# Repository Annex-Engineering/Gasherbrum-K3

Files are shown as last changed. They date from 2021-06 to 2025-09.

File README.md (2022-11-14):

# Gasherbrum (K3) Printer - Release 1.1

Project Gasherbrum (K3 for short) is a Small Format, Direct Drive, Fully Enclosed or Open Air FDM Printer.

This is an entirely scratch design, based on the efforts of the "Hypercube Overkill Project" for the XY Motion System, and inspired by all other prior repraps.

Our discord server can be found here: 

Join me on Discord (https://discord.gg/MzTR3zE)

BOM/Sourcing Guide can be found here: https://docs.google.com/spreadsheets/d/1O3eyVuQ6M4F03MJSDs4Z71_XyNjXL5HFTZr1jsaAtRc/edit?usp=sharing

# Project Goals:
- Fully Enclosed Design or Open Air
- 2020 Frame Members
- Build Volume of ~180^3 mm
- Direct Drive Extruder (Sherpa Mini, Sherpa Micro, and Folded Ascender supported)
- Shortest Belt Paths Possible, 4 Motors, 2 Per X, 2 Per Y Axis
- Moving Bed
- MGN9C Rails (XYZ and Cross)
- 9mm Belts on XYZ
- Maxwell Coupling on Bed Frame
- NEMA17 Motors XYZ
- LDO Stepper Motors (Optional but Recommended)
- Minimal Printed Parts (ABS/ASA Required)
- 32 bit controller standard (Single Fysetc Spider, or Fysetc S6 with expander configurations provided, others at your own leasure) - Klipper Highly Recommended
- 24V Power Standard, 48V Power Optional via the ANNEX Constellation Series of Boards
- AC Heated Bed, MIC6 Plate with Magnetic Build Surface or Glass on Thermal Pads
- Supports many hotends

* Enclosed Printers are passively heated and only designed around an average 65C chamber temperature, K3 is not intended to be a High Temperature printer. It was designed to excell at common engineering materials such as PLA, PETG, ABS and some PC/Nylon Blends

# Images
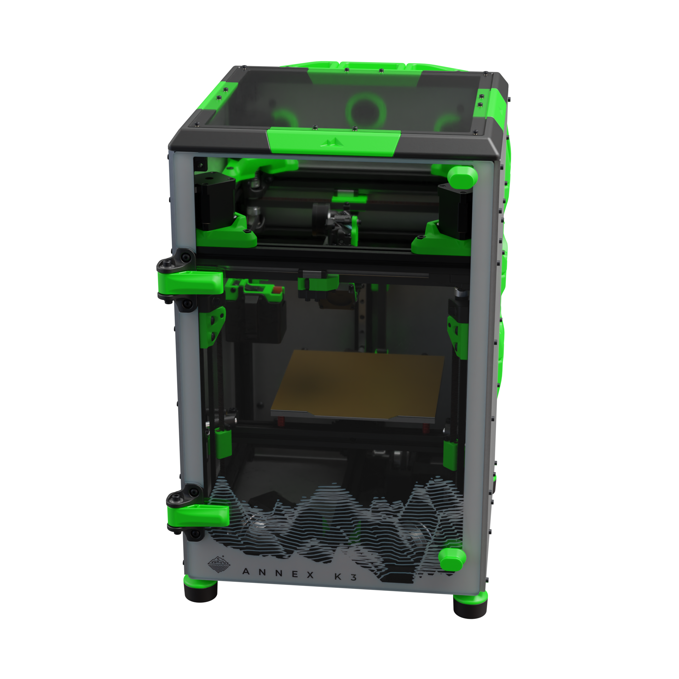
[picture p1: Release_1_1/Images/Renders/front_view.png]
Image of K3
 
  
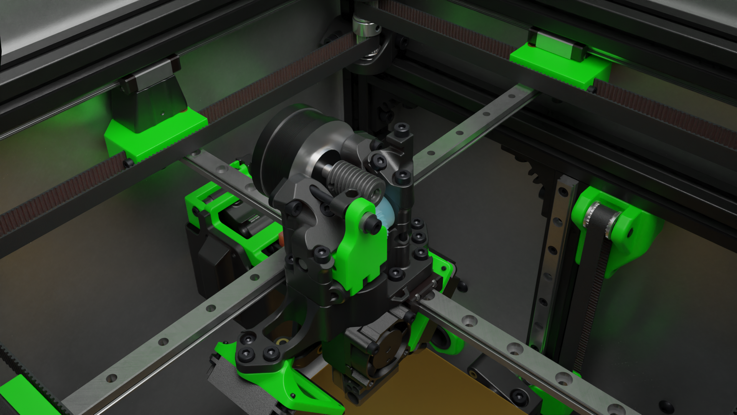
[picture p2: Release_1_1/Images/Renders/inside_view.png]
Image of K3
 

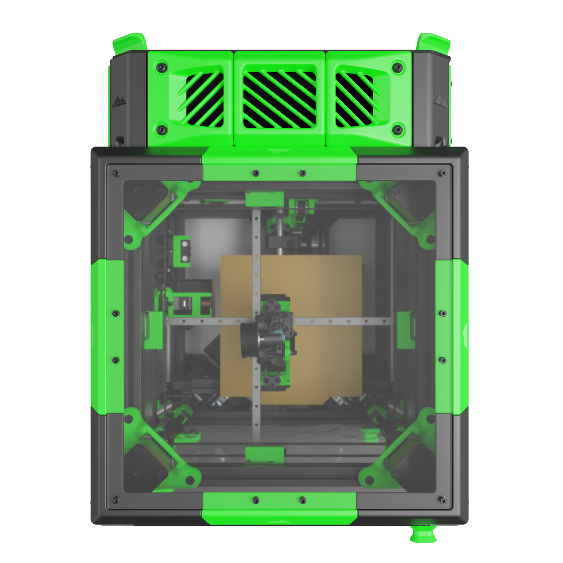
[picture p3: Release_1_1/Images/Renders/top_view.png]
Image of K3


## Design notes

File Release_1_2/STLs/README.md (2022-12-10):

# STL Options

Subfolders containing multiple variants of each part will generally contain a README file that lists which files you need to print for each option. The following sections explain file labels that apply to all STL subfolders in general.

## Extrusion Variants

Extrusions can be tapped as either M5 or M6. Parts with "(m6_thread)" in the filename are meant for extrusions tapped as M6, and parts with the same filename but missing this label are meant for extrusions tapped as M5.

## XY Motor Variants

K3 can be built either with standard motors with a shaft and coupling, or with custom long shaft motors from LDO. Parts with "(custom_LDO_motor_option)" in the filename are meant for use with the custom LDO motors, and parts with the same filename but missing this label are meant for use with standard motors.

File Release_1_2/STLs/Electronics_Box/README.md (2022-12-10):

# R2 Electronics Box Options

The R2 electronics box requires 300mm extrusions for mounting electronics instead of 310mm. If you want to use it with 310mm extrusions, you can print `electronics_box_panel_spacer_x8` from the "optional" folder to space the panels outwards from the corners.

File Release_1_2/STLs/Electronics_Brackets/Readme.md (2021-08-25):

# Electronics Brackets

## Universal Controller Brackets
Supports the following controllers, in a horizontal orientation.
<br> Note: *may support others, these are just the ones that have been checked*

 - Fysetc Spider
 - Fysetc S6
 - BTT SKR 1.3/1.4
 - BTT SKR Pro
 - BTT Octopus
 - Duet Mini 5
 - BTT Motor Expander

## Universal Rpi Brackets
Supports Raspberry Pi 1-4 in vertical or horizontal orientation

## UHP Mounting Brackets
Supports the following power supplies
 - UHP 200 series
 - UHP 350 series
 
## RS Mounting Brackets
Supports the following power supplies
 - RS 25 series
 - RS 35 series

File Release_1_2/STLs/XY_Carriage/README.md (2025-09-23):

# Toolhead Options and Notes

## Useful Notes

- There is an eDrawing for the toolheads that contains a configuration for each
  hotend with sherpa mini, one with sherpa micro and mosquito, and one with
  ascender and mosquito. Click the "Configurations" button in the bottom right
  to access all the configurations.
- Range of motion:
    - X: -8 to 180
    - Y: -2 to 184
- Probe dock location: X-8 Y181
- Homing location: X180 Y-2
- Bowden tube length (mm):

    |               | Sherpa (Mini or Micro)  | Ascender  | LGX Lite  |
    | ---           | ---                     | ---       | ---       |
    | Mosquito      | 26.5                    | 25.5      | 21.5      |
    | VolcoMosq     | 26.5                    | 25.5      | 21.5      |
    | Teakettle     | unknown*                | unknown*  | unknown*  |
    | Dragon        | 27.5                    | 26.5      | 22.5      |
    | Rapido HF     | unknown*                | unknown*  | unknown*  |
    
    - *For each of the hotends with unknown bowden tube length, the bowden tube
      should extend above the main body by the amount shown below, depending on
      which extruder you're using. We do not currently know how far the tube
      extends into these hotends; if you use one of them, please measure the
      overall length of your tube after cutting it so we can add it to this
      guide.
      - Sherpa (Mini or Micro): 8mm
      - Ascender: 7.5mm

- For the Mosquito and VolcoMosq versions, make sure the thickness of the hotend
  fan + the height of the screw head attaching it add up to less than 13.36mm.
- If you use the Rapido, remove the groove mount adapter.
- If you use the Rapido, make sure it is oriented so the wire is exiting in the
  same direction as in the edrawing. Other orientations also work if you use
  M2.5x14 screws to make sure the screw doesn't hit the heatsink.
- Some versions of the toolhead space the fan mounts and probe downward since
  the hotend is longer. With these hotends, you may lose up to the following z
  height:
    - VolcoMosq: 8.5mm
    - Rapido HF: 8.5mm
- There is 1 fan mount hole in the main body that is recessed more than the
  others. This hole requires a button head screw, but the remaining 5 holes can
  be either BHCS or SHCS.
- All versions of the toolhead use a 25mm fan for the hotend, except for the
  Dragon version, which uses a 30mm fan.

## What to print

Please print all parts in the "common parts" section, the section for your
chosen hotend, the section for your chosen extruder, and the section for your
chosen probe:

### Common parts

- `front_fan_mount_x1`
- `front_fan_nozzle_x1`
- `magswitch_probe_mount_x1`
- `omron_d2f-5_microswitch_probe_body_x1`
- `rear_fan_mount_x1`
- `rear_fan_nozzle_x1`

### Hotends

Slice Mosquito
- main body (depends on your extruder):
  - Sherpa Mini: `sherpa_mini_mosquito_main_body_x1`
  - Sherpa Micro: `sherpa_micro_mosquito_main_body_x1`
  - Ascender: `ascender_mosquito_main_body_x1`
  - LGX Lite:
    - `lgx_lite_mosquito_main_body_x1`
    - `lgx_lite_mounting_plate_x1`
- `mosquito_brace_for_probe_mount_x1`
- `mosquito_side_mount_x1`

VolcoMosq
- main body (depends on your extruder):
  - Sherpa Mini: `sherpa_mini_mosquito_main_body_x1`
  - Sherpa Micro: `sherpa_micro_mosquito_main_body_x1`
  - Ascender: `ascender_mosquito_main_body_x1`
  - LGX Lite:
    - `lgx_lite_mosquito_main_body_x1`
    - `lgx_lite_mounting_plate_x1`
- `mosquito_side_mount_x1`
- `volcomosq_brace_for_probe_mount_x1`
- `volcomosq_fan_spacer_x2`

Teakettle
- main body (depends on your extruder):
  - Sherpa Mini: `sherpa_mini_teakettle_main_body_x1`
  - Sherpa Micro: `sherpa_micro_teakettle_main_body_x1`
  - Ascender: `ascender_teakettle_main_body_x1`
- `teakettle_brace_for_probe_mount_x1`
- `teakettle_fan_shroud_outlet_x1`
- `rail_cart_screw_spacer_0.5mm_x1`
  - If your rail cart screw holes are tapped to at least 3.5mm deep, you can
    omit this part.

Dragon-Style Hotend
- main body (depends on your extruder):
  - Sherpa Mini: `sherpa_mini_dragon_main_body_x1`
  - Sherpa Micro: `sherpa_micro_dragon_main_body_x1`
  - Ascender: `ascender_dragon_main_body_x1`
  - LGX Lite:
    - `lgx_lite_dragon_main_body_x1`
    - `lgx_lite_mounting_plate_x1`
- `dragon_brace_for_probe_mount_x1`
- `dragon_fan_shroud_x1`

Rapido HF
- main body (depends on your extruder):
  - Sherpa Mini: `sherpa_mini_dragon_main_body_x1`
  - Sherpa Micro: `sherpa_micro_dragon_main_body_x1`
  - Ascender: `ascender_dragon_main_body_x1`
  - LGX Lite:
    - `lgx_lite_dragon_main_body_x1`
    - `lgx_lite_mounting_plate_x1`
- `volcomosq_brace_for_probe_mount_x1`
- `volcomosq_fan_spacer_x2`
- `rapido_fan_shroud_x1`

### Extruders

Sherpa Mini
- `sherpa_umbilical_mount_x1`
- (sherpa mini extruder with k-series front housing)

Sherpa Micro
- `sherpa_umbilical_mount_x1`
- (sherpa micro extruder with k-series front housing)

Ascender
- `ascender_umbilical_mount_x1`
- (double folded ascender extruder - R4 or newer)

LGX Lite
- `lgx_lite_umbilical_mount_x1`

### Probes

Beacon RevH
- `beacon_mount_(revH)_x1`

Beacon RevD
- `beacon_mount_(revD)_x1`

Quickdraw
- `magswitch_probe_mount_x1`
- `omron_d2f-5_microswitch_probe_body_x1`

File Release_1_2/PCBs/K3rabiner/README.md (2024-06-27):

# K3rabiner-Toolboard

The K3rabiner is a toolboard for the K3 and an easy & quick connection between the backpack and toolhead. Thanks to wendemann for the original work.
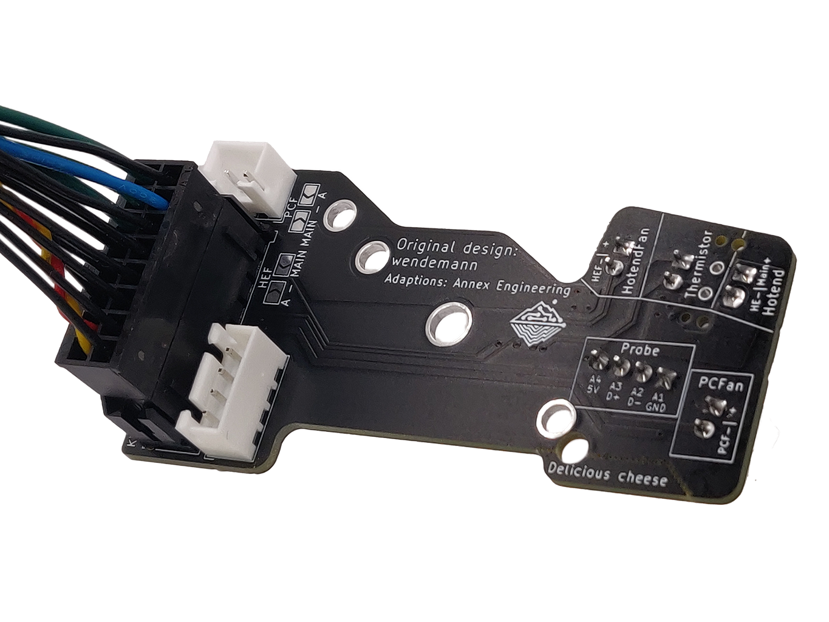
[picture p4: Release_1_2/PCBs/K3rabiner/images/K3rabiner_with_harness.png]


## Features

- Supports Sherpa mini/micro ONLY
- Input via 16pin horizontal microfit
- Output for partcooling fans
- Soldered seperate voltage selection for hotend fan and partcooling fan
   - Uses either the hotend voltage or one alternative voltage

## Connectors & Amperage

_Note: All amperage-values have been designed to work in an enclosed printer with up to 65° chamber temperature & have  some safety margins. While you could use higher ampere in an open-frame printer, it's highly discouraged. <br/>
When multiple connectors are supported **bold** marks the recommended connector._

| | Supported Connectors | Maximum Ampere |
| --- | --- | --- |
| Hotend  | 2-pin JST XH <br/> Microfit 430450227 <br/> **Microfit 436500227** (compatible with e3d heater) | ~2 Ampere (50W heater on 24V) <br/> 4.2 Ampere (100W heater on 24V) <br/>4.2 Ampere (100W heater on 24V)
| Hotend Thermistor  | 2-pin JST XH <br/> **Microfit 436500227** (compatible with e3d thermistor) | / <br/> /
| Hotend Fan | 2-pin JST XH | 1 Ampere
| Partcooling Fan | 2-pin JST XH | 2 Ampere
| Stepper | 4-pin JST XH | 1.2 Ampere <br/> 0.84 Ampere on TMC drivers as you specify the RMS ampere which is ~70% of peak
| Aux / Probe | 4-pin JST XH | 0.8 Ampere

## Sourcing
Links to purchase fully assembled boards can be found here: [ANNEX Sourcing Guide](https://docs.google.com/spreadsheets/d/1aSM1jGxg-s0tyynyR3f8M0IQMXuXw57RJvoJbt98Clw/edit?usp=sharing)

Be aware that K3rabiner B0.1 and up have 3 different options for Heater and Thermistor connectors:
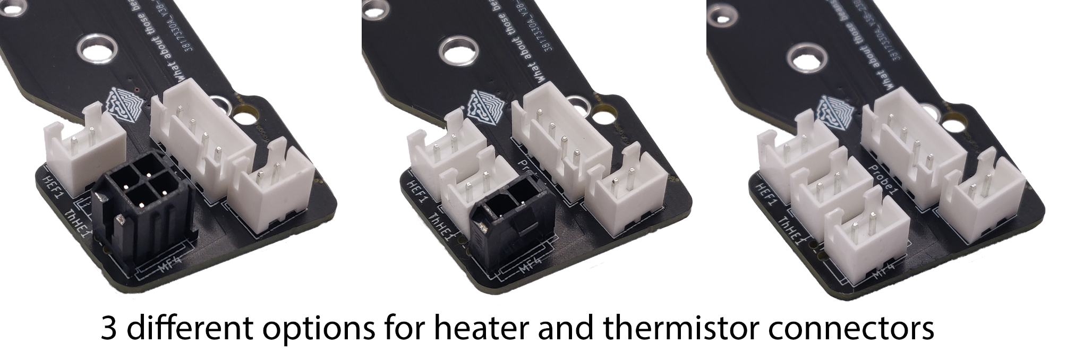
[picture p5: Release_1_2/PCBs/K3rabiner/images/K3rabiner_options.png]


## Wiring Guide

This pinout assumes you're looking directly at the cable. 

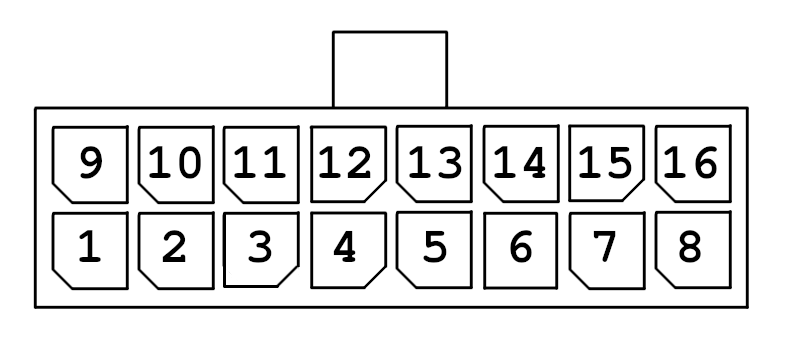
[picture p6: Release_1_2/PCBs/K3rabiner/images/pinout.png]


| PinNumber | Usage | PinNumber | Usage |
|---|:---:| --- |:---:|
| 1  |  Thermistor Chamber | 9 | Hotend Voltage
| 2  | Partcooling Fans Ground | 10 | Hotend Ground
| 3  | Hotend Fan Ground | 11 | Alt Voltage
| 4  | Thermistor Common Ground | 12 | Thermistor Hotend
| 5  | Motor A | 13 | Motor C
| 6  | Motor B | 14 | Motor D
| 7  | Aux 1 | 15 | Aux 2
| 8  | Aux 4 | 16 | Aux 3

## Gallery
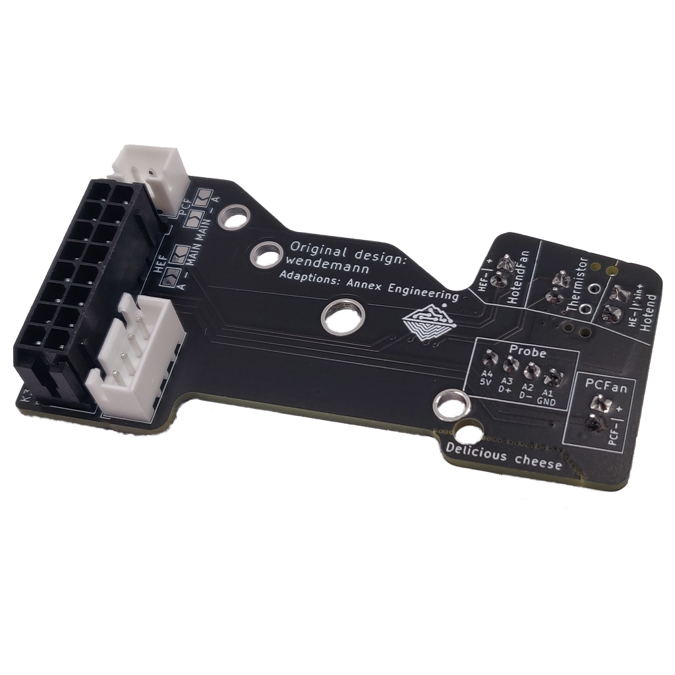
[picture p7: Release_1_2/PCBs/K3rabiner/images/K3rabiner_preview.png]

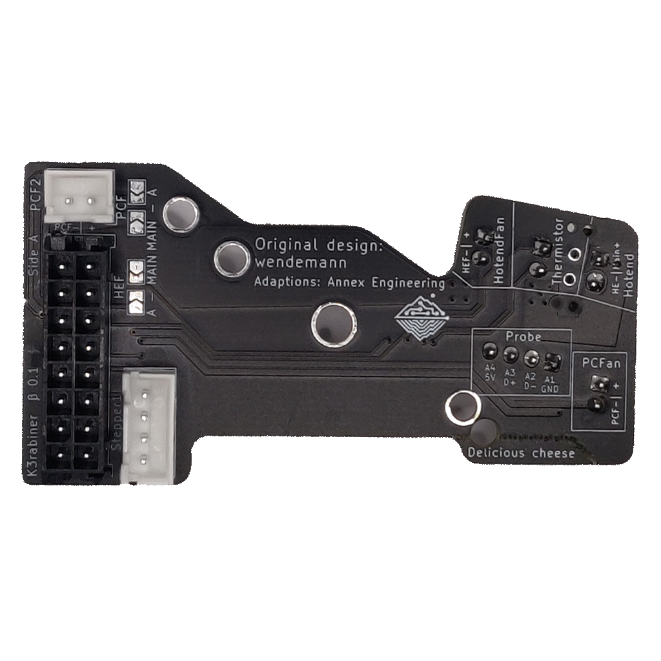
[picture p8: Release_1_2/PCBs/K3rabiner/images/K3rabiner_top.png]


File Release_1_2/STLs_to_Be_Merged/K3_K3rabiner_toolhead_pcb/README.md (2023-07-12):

# K3rabiner-Toolboard

The K3rabiner is a toolboard for the K3 and an easy & quick connection between the backpack and toolhead. Thanks to wendemann for the original work.


## Features and Notes

- K3rabiner will be the toolhead path moving forward, all future designs will use it in some form or another due to packaging constraints. This may result in support for some hotends being dropped and/or some extruders being temporarily unsupported (folded ascender) while we get our shit together.
- Supports Sherpa mini/micro ONLY
- Input via 16pin horizontal microfit
- Output for partcooling fans
- Soldered seperate voltage selection for hotend fan and partcooling fan
   - Uses either the hotend voltage or one alternative voltage

## Latest information
The latest information related to the pcb can be found [HERE.](https://github.com/Annex-Engineering/Annex_Engineering_PCBs/tree/master/carabiner-series-toolboard/k3rabiner)

## Sourcing
Links to purchase fully assembled boards can be found here: [ANNEX Sourcing Guide](https://docs.google.com/spreadsheets/d/1aSM1jGxg-s0tyynyR3f8M0IQMXuXw57RJvoJbt98Clw/edit?usp=sharing)

## Gallery
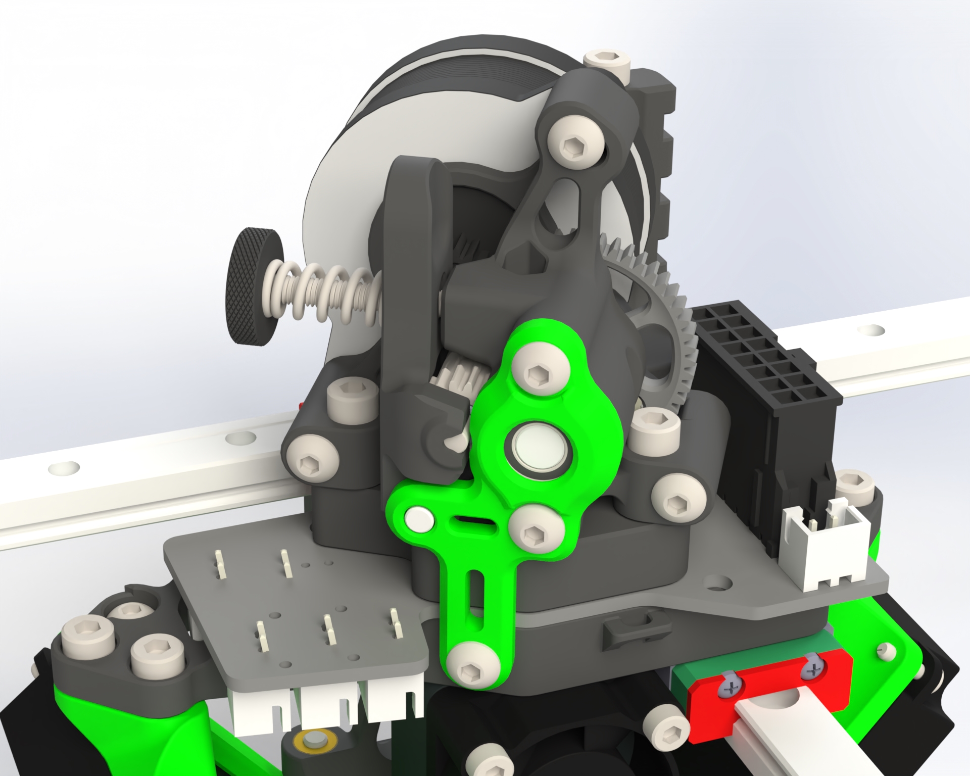
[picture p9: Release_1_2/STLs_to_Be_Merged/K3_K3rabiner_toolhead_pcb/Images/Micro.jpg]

K3rabiner with the Sherpa Micro

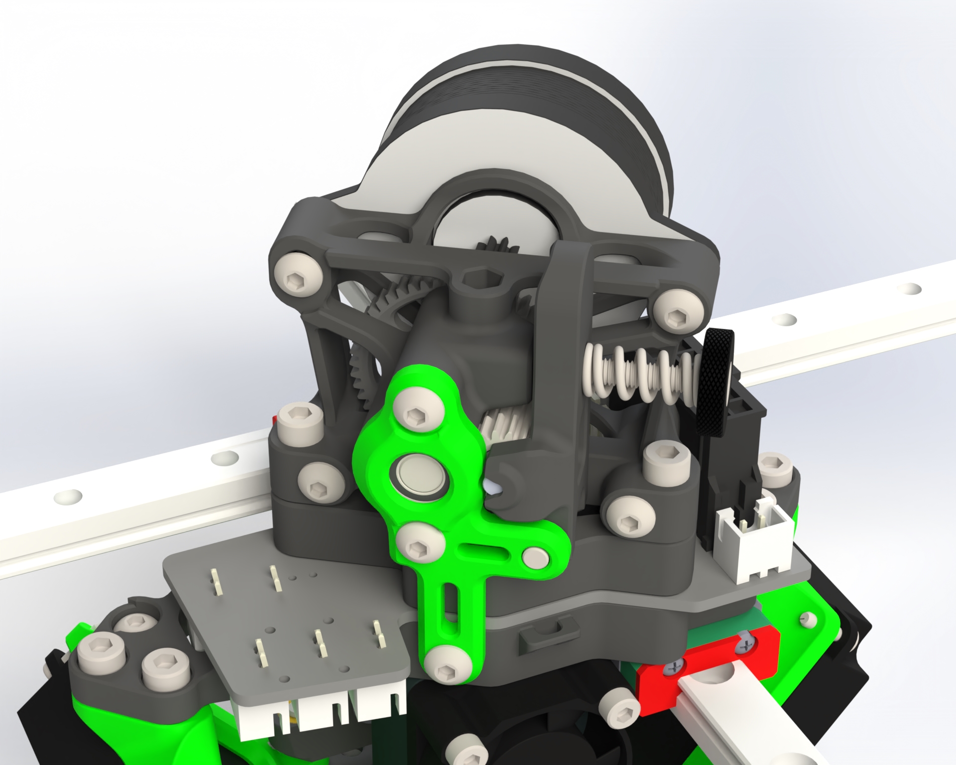
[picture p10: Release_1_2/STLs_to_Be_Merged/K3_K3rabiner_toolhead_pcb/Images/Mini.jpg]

K3rabiner with the Sherpa Mini

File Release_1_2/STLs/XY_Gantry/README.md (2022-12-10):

XY Gantry Options
=================

## Linear Rail Instructions

### Running RobotDigg or LDO Rails? ###

If you are using RobotDigg or LDO rails, you should to use the STLs in the `for_6.0mm_thick_rails` folder for the tensioner spacer and rail mounts, as these rails are 0.5mm thinner.

### Spacer Sizing Tips ###

- Before printing the tensioner spacer, try slicing the main toolhead plate (with whatever settings you will/did use to print it) and check the distance from the bottom to the surface that sits underneath the upside-down rail. The model is 6.5mm thick, but depending on your slicer and its settings, the part may be sliced slightly thicker or thinner.
- Try slicing the tensioner spacer and check it's sliced height from top to bottom.
    - For 6.5mm (normal) rails, the spacer height should be 13.5mm thicker than the toolhead plate measurement.
    - For 6.0mm (Robotdigg) rails, the spacer height should be 14.0mm thicker than the toolhead plate measurement
    - For example, if the toolhead plate slices at 6.6mm thick and you're using Robotdigg rails, size the spacers so that they are sliced 20.6mm tall.
- Scale the tensioner spacer (in the z axis only) if it is the wrong size when sliced.
- For best alignment of the final assembly, you may choose to physically measure the toolhead plate after printing it, then print the spacers with an extra layer and carefully sand them down to final dimension. Be sure to keep the top and bottom surfaces flat and parallel when sanding.

## XY Shim Placement

The number of shims to place in the x- and y-axis drive stacks depends on the overall height of your idlers (either 13mm or 14mm). The eDrawing shows xy corner drives with 14mm idlers. The table below shows the shim height needed at each location:

| | 13mm Idlers | 14mm Idlers |
| --- | --- | --- |
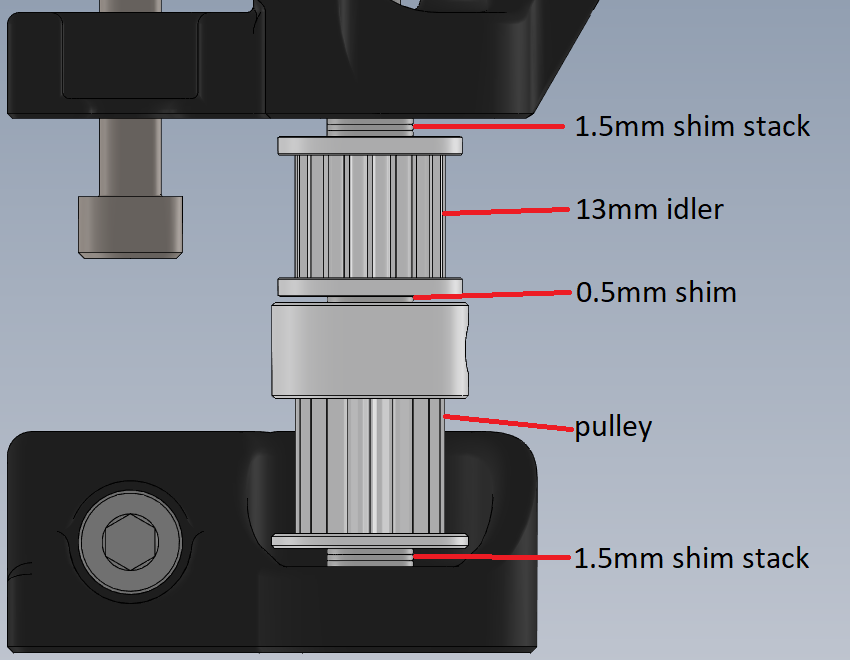
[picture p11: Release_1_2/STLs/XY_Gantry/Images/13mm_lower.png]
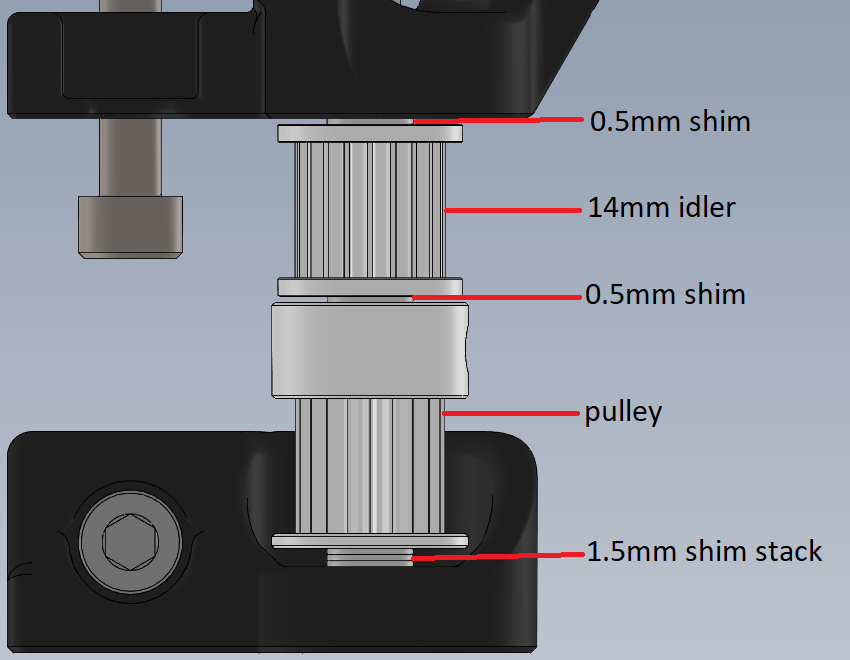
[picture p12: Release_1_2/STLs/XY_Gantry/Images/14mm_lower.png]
| Idler on top |  |  |
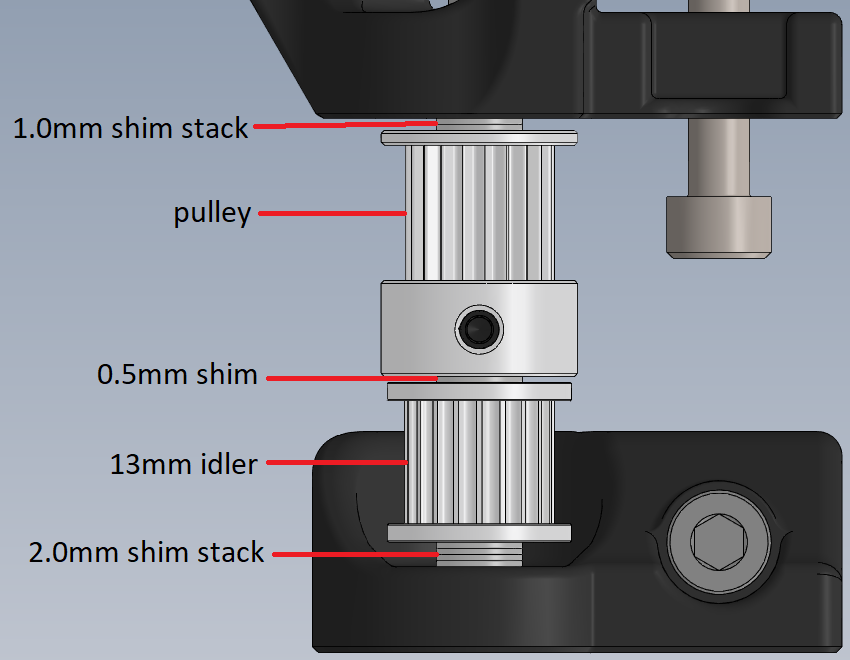
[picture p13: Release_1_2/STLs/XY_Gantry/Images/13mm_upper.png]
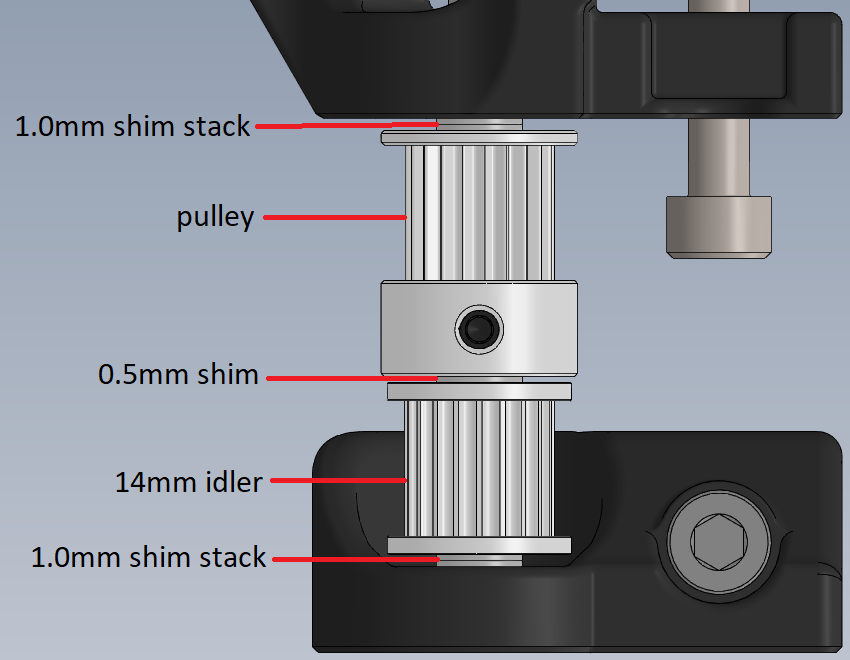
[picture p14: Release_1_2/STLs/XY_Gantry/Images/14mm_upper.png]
| Idler on bottom |  |  |

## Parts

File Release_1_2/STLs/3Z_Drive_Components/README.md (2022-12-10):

# 3Z Drive Options

If using a VolcoMosq, Dragonfly HIC, or Rapido hotend, print the `z_idler_rear_x1` stl from the `for_long_hotends` folder instead of the one in this folder.

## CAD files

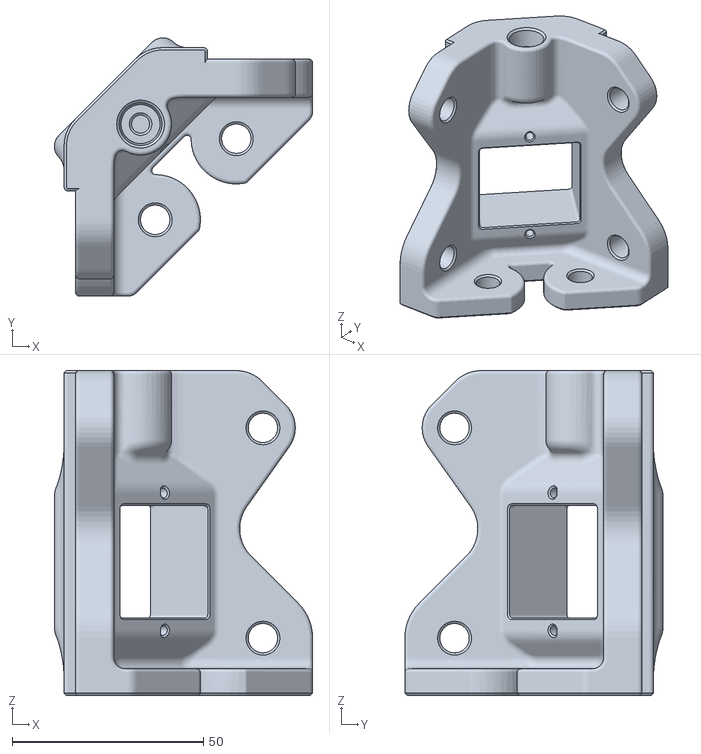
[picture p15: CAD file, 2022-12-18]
Release_1_2/STLs/Electronics_Box/electronics_box_corner_mains_inlet_x1_rev4.STL
67.6 x 67.6 x 85.0

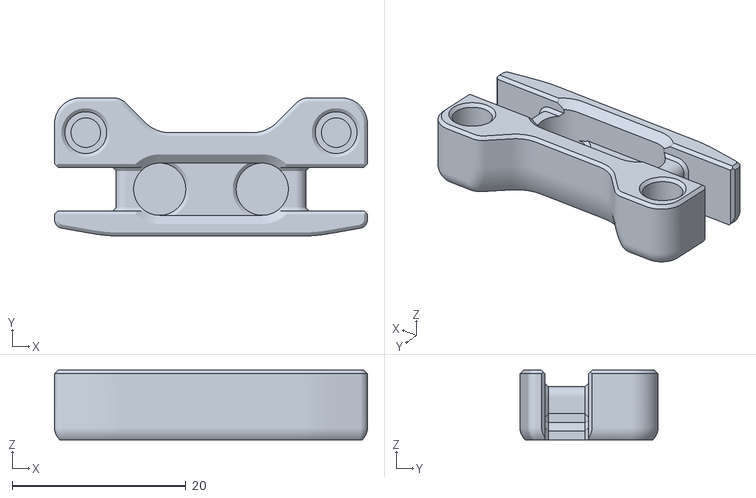
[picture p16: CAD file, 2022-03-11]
Release_1_2/STLs/Probe_Dock_and_Purge_Bucket/[a]_microswitch_probe_dock_main_x1_rev1.STL
36.0 x 15.9 x 8.00

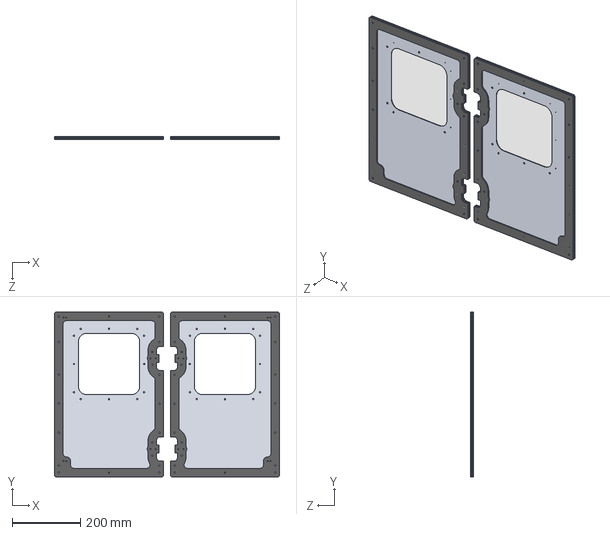
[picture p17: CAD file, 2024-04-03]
Release_1_1/CAD/Kseries_Front_Door_Parametric-High_Temp.STEP
660.0 x 483.0 x 9.00 mm

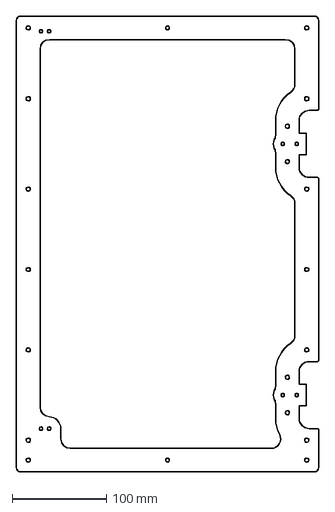
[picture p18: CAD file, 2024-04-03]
Release_1_1/DXFs/High_Temp_Door_with_Window/Front_Door_180mm_x_180mm_Gasket_x2_Rev1.DXF
320.0 x 483.0 mm

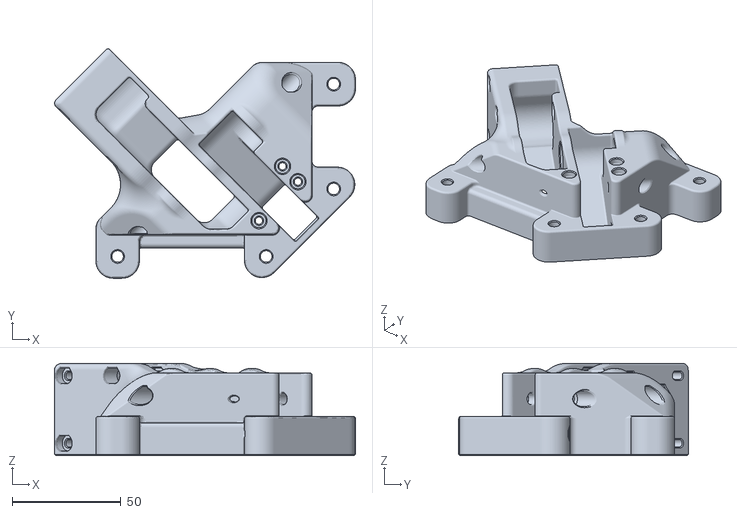
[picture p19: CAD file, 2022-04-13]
Release_1_1/STLs/3Z_Drive_Components/z_drive_front_right_x1_rev3.stl
138.2 x 105.4 x 42.3

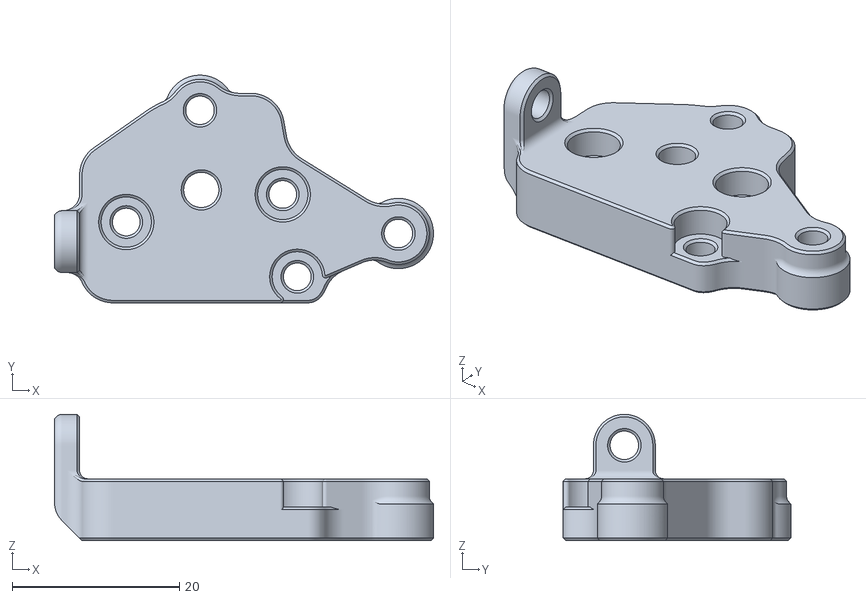
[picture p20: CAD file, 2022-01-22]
Release_1_1/STLs/XY_Carriage/[a]_lgx_lite_mounting_plate_x1_rev1.stl
45.3 x 27.2 x 15.1

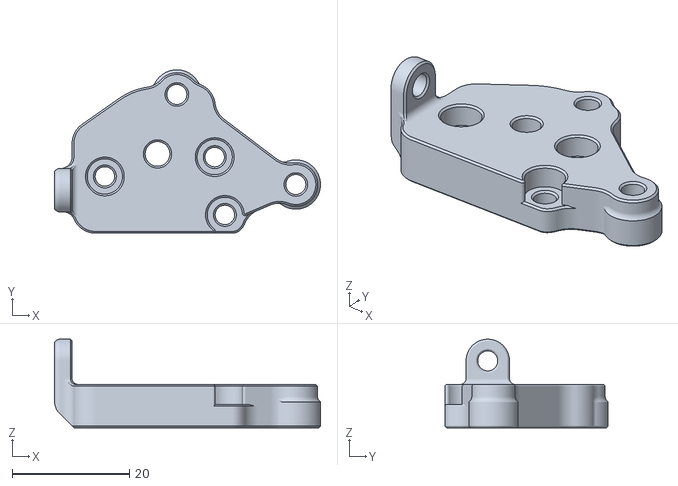
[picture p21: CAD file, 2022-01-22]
Release_1_1/STLs/XY_Carriage/dragonfly_bmo_hotend/[a]_lgx_lite_dragonfly_bmo_mounting_plate_x1_rev1.stl
45.3 x 27.8 x 15.1

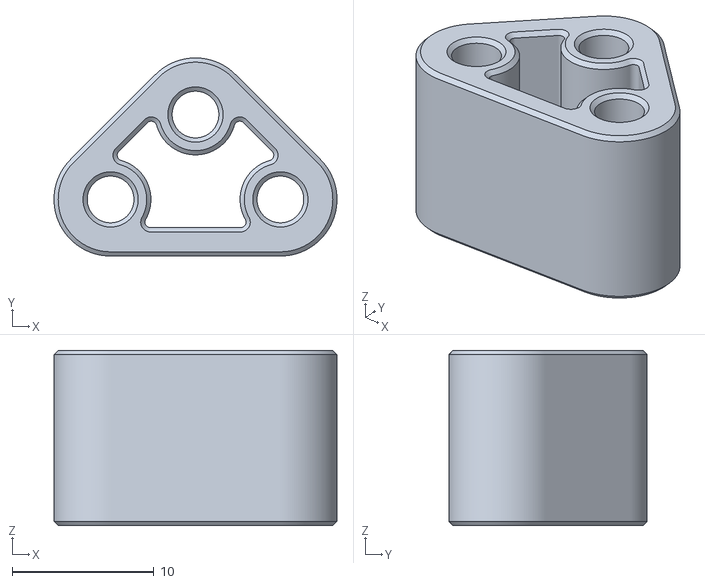
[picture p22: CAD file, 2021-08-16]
Release_1_1/STLs/XY_Carriage/dragonfly_hic_hotend/[a]_dragonfly_hic_fan_spacer_x2_rev2.stl
20.0 x 14.0 x 12.4

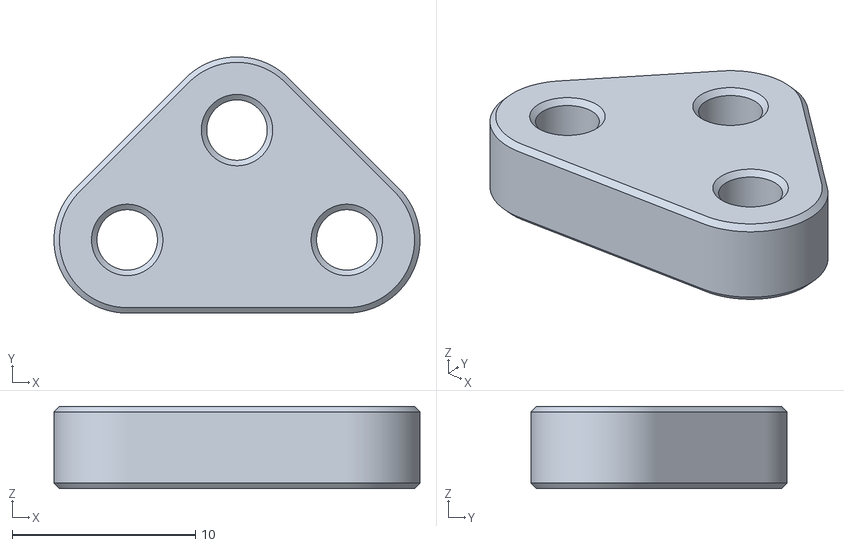
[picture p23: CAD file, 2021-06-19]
Release_1_1/STLs/XY_Carriage/slice_copperhead_hotend/[a]_copperhead_fan_spacer_x2_rev1.stl
20.0 x 14.0 x 4.50

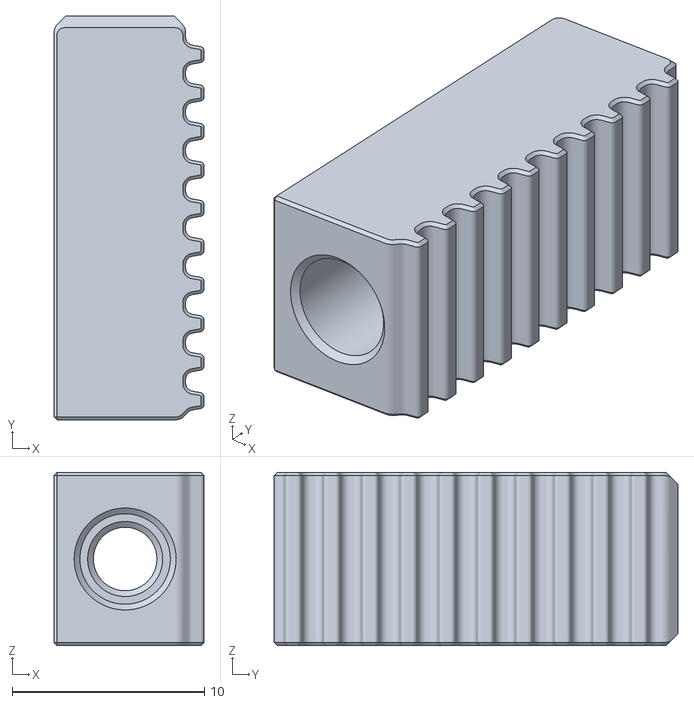
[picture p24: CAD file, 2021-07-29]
Release_1_1/STLs/XY_Gantry/[a]_xy_tensioner_moving_x8_rev3.stl
7.80 x 21.0 x 9.00

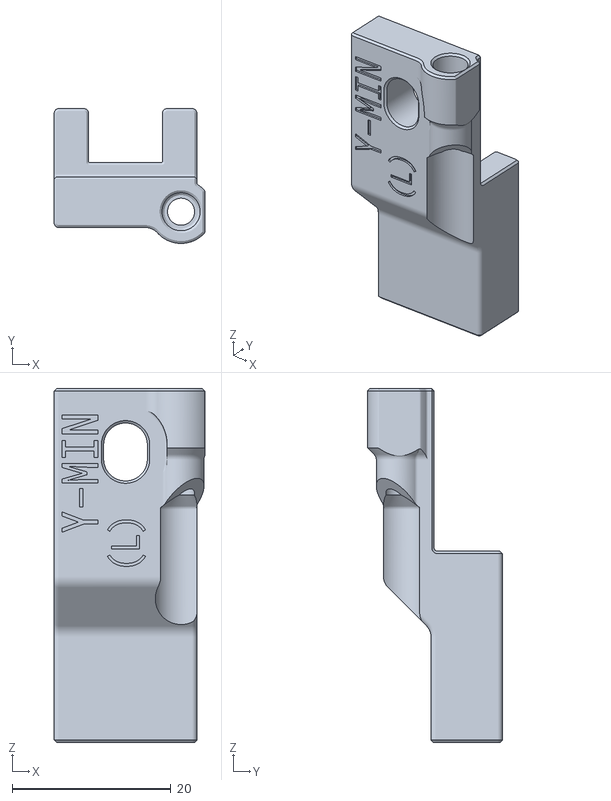
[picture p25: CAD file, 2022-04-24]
Release_1_1/STLs/XY_Gantry/split_corner_drive_endstops/y_min_left_split corner_endstop_x1_rev3.stl
19.0 x 17.0 x 44.6

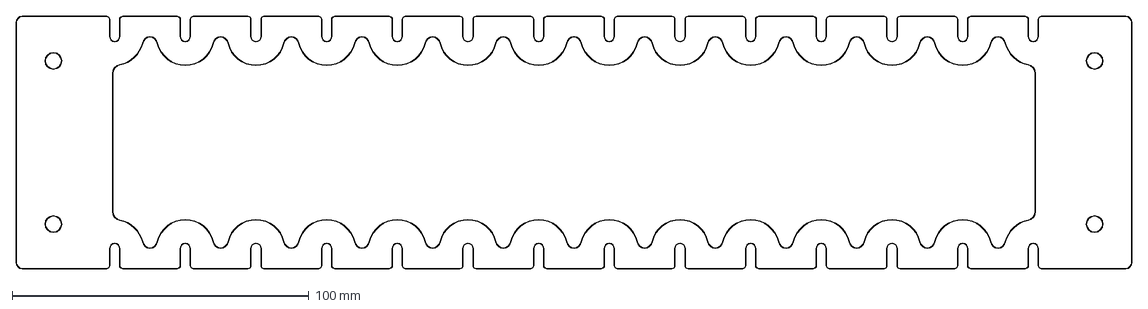
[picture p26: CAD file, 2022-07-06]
Release_1_2/DXFs/Ebox/electronics_box_side_structural_panel_x2_rev1.DXF
376.2 x 85.0 mm

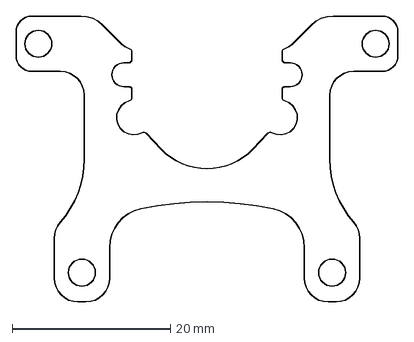
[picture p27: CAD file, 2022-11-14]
Release_1_2/DXFs/Mosquito Net/K3_Mosquito_Net_x1_Rev1_1.2mm_Stainless_Steel.DXF
48.2 x 36.1 mm

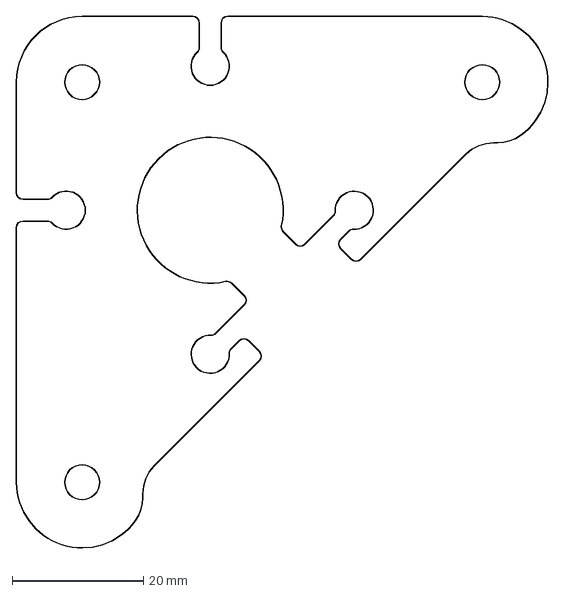
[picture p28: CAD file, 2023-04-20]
Release_1_2/DXFs/Motor_Mounts/corner_motor_mount_ldo_bottom_rev3_x4_6mm_mild_steel.DXF
81.8 x 81.8 mm

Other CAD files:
Release_1_2/DXFs/Panels/Back_Panel_180mm_x_180mm_x1_Rev3.DXF
Release_1_2/DXFs/Thermal_Backers_for_XY_Rails/K3_2020_Backer_2.6mm_mild_steel_x4_rev1.dxf
Release_1_2/STLs/3Z_Drive_Components/[a]_z_tensioner_moving_moar_grip_x3_rev1.stl
Release_1_2/STLs/3Z_Drive_Components/for_long_hotends/[a]_z_idler_rear_(lowered)_x1_rev3.stl
Archive/Release_1/CAD/Electronics_Box_Blanking_Plate.STEP
Archive/Release_1/CAD/Electronics_Box_Blanking_Plate.x_t
Archive/Release_1/DXFs/Electronics_Box/Full_Height_(Optional_for_Summit_Only)/electronics_box_bottom_&_top_panel_decorative_x2_rev1.DXF
Archive/Release_1/DXFs/Electronics_Box/Full_Height_(Optional_for_Summit_Only)/electronics_box_cover_x1_rev1.DXF
Archive/Release_1/DXFs/Electronics_Box/Full_Height_(Optional_for_Summit_Only)/electronics_box_side_panel_decorative_x1_rev1.DXF
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

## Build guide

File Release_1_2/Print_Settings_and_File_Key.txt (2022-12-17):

Primary Color: nothing at start of file name
Accent Color: [a]_ at start of file name
Quantity Required: _x# near end of file name
File Revision: _Rev# at end of file name

Nozzle Size: 0.5mm 
Recommended FDM Materials: ASA, Polymaker or 3DXTech Recommended
Alternate Approved FDM Materials: PC, 3DXTech Recommended
Layer Height: 0.25mm
Extrusion Width: Forced 0.5mm
Infill Percentage: 40% minimum (at 0.8mm Width)
Infill Type: Grid, Gyroid, Honeycomb, Triangle or Cubic
Wall Count: 3 minimum (at 0.5mm Width)
Solid Top/Bottom Layers: 4 minimum (at 0.5mm Height)

Nozzle Size: 0.4mm 
Recommended FDM Materials: ASA, Polymaker or 3DXTech Recommended
Alternate Approved FDM Materials: PC, 3DXTech Recommended
Layer Height: 0.20mm or 0.25mm
Extrusion Width: Forced 0.4mm
Infill Percentage: 40% minimum (at 0.6mm Width)
Infill Type: Grid, Gyroid, Honeycomb, Triangle or Cubic
Wall Count: 4 minimum (at 0.4mm Width)
Solid Top/Bottom Layers: 4 minimum (at 0.25mm Height)

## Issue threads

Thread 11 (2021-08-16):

CAD release date

Rudis1261, 2021-08-16:
Hi Guys, loving building the printer so far, just waiting on the slow boat from China.

Any idea when the CAD for the printer will be released? I am quite keen to create a hotend mount for my orbiter straight from source if possible. Along with some minor tweaks to suite my needs.

Cheers

Rudis1261, 2021-08-17:
For example, I am struggling to find the right size heat inserts, so would be nice to be able to modify those parts

Annex-Engineering, 2021-08-18:
TLDR: we dont do cad releases on beta machines, theres a lot of reasons behind it, and it would take me 2 pages to cover them all

sadly, an orbiter will not fit on the K3, youll lose 20mm of x and y travel because of it. We highly recommend you use our extruders instead, as they are lighter and perform better.

Have you tried the sourcing guide for the heatsets?

Rudis1261, 2021-08-18:
The heat set inserts on the sourcing guide (aliexpress) is very expensive to ship $130 just in shipping. It's a bit on the rough side.  So I am forced to edit the STL files which can be a tad painful, but I understand you have your reasons.

I have printed the Sherpa, and slapped in some bondtech gears in there, so hope to keep making progress on the build.

Any ETA (ballpark) on when the printer will come out of beta?

Annex-Engineering, 2021-08-18:
we dont have an ETA for any release, we dont like putting timelines on things because it tends to create sloppy work (and its all a hobby for everyone here, so the last thing they need is to be stressed about it)

Rudis1261, 2021-08-18:
Fair enough. Keep up the great work, cant wait to also have a working K3.

Really impression with your innovative design!

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

Closed 2021-08-18.

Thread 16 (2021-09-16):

Screw Z part in common folder

Rudis1261, 2021-09-16:
Hey guys,

Can you please move this file:
https://github.com/Annex-Engineering/Gasherbrum-K3/blob/main/STLs/3Z_Drive_Components/common_parts/safety_spring_mount_rear_x1_rev2.stl

To this folder?
https://github.com/Annex-Engineering/Gasherbrum-K3/tree/main/STLs/3Z_Drive_Components/tr12_screw_drive

It's for the screw z

LeandroMarceddu, 2021-09-16:
#15

Closed 2021-09-16.

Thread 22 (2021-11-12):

Humps that slot into alu extrusions do not match

amp-man, 2021-11-12:
The little humps that fit into the alu extrusion slots are wider than the rest of the K3 parts.
The following parts that I found have the wider hump:
- front_door_bearing_block_1_x2_rev1.STL
- front_door_bearing_block_2_x2_rev1.STL
- front_door_magnet_catch_x1_rev1.STL
It would be great if you could make the hump of these parts smaller, e.g. make them the same as the rest of the parts.
The smaller hump seems to work fine for all other K3 Parts and have the benefit that they also work for I type 5mm extrusion.

Trails5000, 2021-11-19:
added files with this commit: [e80344b860d09d5b334a637461350ae481a8b810](https://github.com/Annex-Engineering/Gasherbrum-K3/commit/e80344b860d09d5b334a637461350ae481a8b810)

amp-man, 2021-11-20:
Thanks :)

Closed 2021-11-19.

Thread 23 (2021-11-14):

Bed frame mount recess for heated insert.

Rudis1261, 2021-11-14:
A nice-to-have for this mount **bed_frame_mount_front** would be to have a small recess to allow the heat-set insert to lay down in. And then you can insert a bolt from the back that screws into it cleanly.

Making it a bit easier to pull the heatset insert into the part. As you only have to heat it to pull it in.

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

Closed 2021-12-10.

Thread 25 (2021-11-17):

5x8x1 washers missing in sourcing guide

Zaglim, 2021-11-17:
Hi,

The sourcing guide has yet to have 5x8x1 washers in it. A filter search of "Washer, 5x8x1" in the eDrawing shows 12 such washers common to both configurations, and 12 more for the belt-Z config.
None unique to the screw config.

I hope this is the right place to let the Annex team know!

Trails5000, 2021-11-19:
added, thanks

Closed 2021-11-19.

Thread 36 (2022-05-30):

Custom silicone heater wires may interfere with purge bucket

rsghosh, 2022-05-30:
With the current design, the wires on the custom silicone heater exit on the left side of the bed and may collide with the purge bucket unless they are bent at a sharp angle. Moving the wires to the right side of the bed (left side in the custom heater drawing) should solve this.

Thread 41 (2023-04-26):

File K3 - R1.1 - 2022-11-24.rar

gcastle2007, 2023-04-26:
Hi,

Is file [K3 - R1.1 - 2022-11-24.rar](https://github.com/Annex-Engineering/Gasherbrum-K3/blob/main/Release_1_1/CAD/K3%20-%20R1.1%20-%202022-11-24.rar) broken? If you open the CAD, it is almost empty.

Closed 2023-07-15.

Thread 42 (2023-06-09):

XY Endstop(X Max) incorrect size in CAD

jyoorepo, 2023-06-09:
XY Endstop(X Max) screw shows "socket head cap screw_am(B18.3.1M - 3 x 0.5 x 45 Hex SHCS -- 18NHX)" but isn't this supposed to be m5x20mm?
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

PapeJelly, 2023-08-23:
Its fixed in the upcoming K3 manual 👍

Closed 2023-08-23.

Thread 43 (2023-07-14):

Minor R1.2 STL issues

ruiqimao, 2023-07-14:
A couple of issues I've found while printing parts:

- [[a]_xy_tensioner_moving_moar_grip_x8_rev1.stl](https://github.com/Annex-Engineering/Gasherbrum-K3/blob/main/Release_1_2/STLs/XY_Gantry/%5Ba%5D_xy_tensioner_moving_moar_grip_x8_rev1.stl) indicates that 8 copies should be printed. However, now that [[a]_z_tensioner_moving_moar_grip_x3_rev1.stl](https://github.com/Annex-Engineering/Gasherbrum-K3/blob/main/Release_1_2/STLs/3Z_Drive_Components/%5Ba%5D_z_tensioner_moving_moar_grip_x3_rev1.stl) exists, there should only be 4 copies needed, or 5 for 1 extra.
- [[a]_corner_motor_mount_2_piece_upper_x4_rev6.stl](https://github.com/Annex-Engineering/Gasherbrum-K3/blob/main/Release_1_2/STLs/XY_Gantry/%5Ba%5D_corner_motor_mount_2_piece_upper_x4_rev6.stl) and [corner_motor_mount_2_piece_upper_x4_rev4.stl](https://github.com/Annex-Engineering/Gasherbrum-K3/blob/main/Release_1_2/STLs/XY_Gantry/corner_motor_mount_2_piece_upper_x4_rev4.stl) share a name, despite serving entirely different functions.
- [x_max_split_corner_endstop_x2_rev3.stl](https://github.com/Annex-Engineering/Gasherbrum-K3/blob/main/Release_1_2/STLs/XY_Gantry/x_max_split_corner_endstop_x2_rev3.stl), [y_min_left_split corner_endstop_x1_rev4.stl](https://github.com/Annex-Engineering/Gasherbrum-K3/blob/main/Release_1_2/STLs/XY_Gantry/y_min_left_split%20corner_endstop_x1_rev4.stl), and [y_min_right_split corner_endstop_x1_rev4.stl](https://github.com/Annex-Engineering/Gasherbrum-K3/blob/main/Release_1_2/STLs/XY_Gantry/y_min_right_split%20corner_endstop_x1_rev4.stl) appear to be oriented incorrectly.

Trails5000, 2023-07-15:
the 8 copies is intentional, some people have issues with them splitting or installing the inserts. Its minimal plastic and worth having spares

the rest are fixed

Closed 2023-07-15.

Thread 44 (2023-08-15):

STEP files for CAD

apoorv1in, 2023-08-15:
Is there a plan to release the CAD files in Step format or a format that is widely used?
It is a big letdown seeing x_t file format, I believe most of diy community uses step format which can be opened and edited in most of opensource CAD software.
Kindly consider this suggestion, If you really want the design to be mass adopted. Take the hint from Voron, I am not asking for detailed documentation just the CAD

whattheflukz, 2023-08-23:
Skill issue, Onshape can import X_T

Trails5000, 2023-08-23:
flukz closed this but im going to expand on it, because  you probably dont have a design background where your daily into and out of CAD.

STEP is considered to be a lossy format, it tends to randomly lose surfaces and require alot of repair upon import. This is something that fusion ignores. It also doesnt help that most of the CAD companies cant seem to agree on standards for step, what is exported out of solidworks is not the same as what is exported out of fusion.

Therefore, we share "native engine cad" only. Most of the dev team works in solidworks, which is powered by the parasolid engine. X_T files are basically native files with the file tree and all personally identifying data stripped out.

TLDR: step sucks, move onto a better format.

Closed 2023-08-23.

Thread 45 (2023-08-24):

K3 Y axis left and right endstops are functionally identical and can be merged

everycoloryouare, 2023-08-24:
With the removal of the extra adjustment screw on the Y axis endstops, the two parts are now identical except for the embossed text. The two parts could be merged into a single file with quantity 2 to reduce stl count.

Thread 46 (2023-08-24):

Potential R1.2 Z axis carriage mount changes

everycoloryouare, 2023-08-24:
There are two potential issues with the current z axis carriage mounts that could be changed for the R1.2 release.

1. The rear z carriage mount has the tension slot shallower than the front mounts. The moving tensioner was made longer and the front parts were changed accordingly, but the rear was not.

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

The rear mount should be lengthened to match the front, otherwise the tensioner sticks out quite a bit.

2. The new counterbored holes on the front carriage mount have very thin geometry near the outter edge. This causes very thin webbing when printed which breaks off easily. The webbing could be removed and chamfered vertically to blend into the top and bottom.

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

Printed parts with webbing broken off and blended with a file:
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

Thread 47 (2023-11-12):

Wrong pulley size in the manual

memphisdj, 2023-11-12:
On the picture below, the pulley should be 6mm and not 9mm. It's wrong on all 3 Z steppers.

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

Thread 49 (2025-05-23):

Broken link in BOM - "Thermal Fuse (125C Cutoff)"

NeighNeighNeigh, 2025-05-23:
The "Thermal Fuse (125C Cutoff)" in the BOM is a broken link

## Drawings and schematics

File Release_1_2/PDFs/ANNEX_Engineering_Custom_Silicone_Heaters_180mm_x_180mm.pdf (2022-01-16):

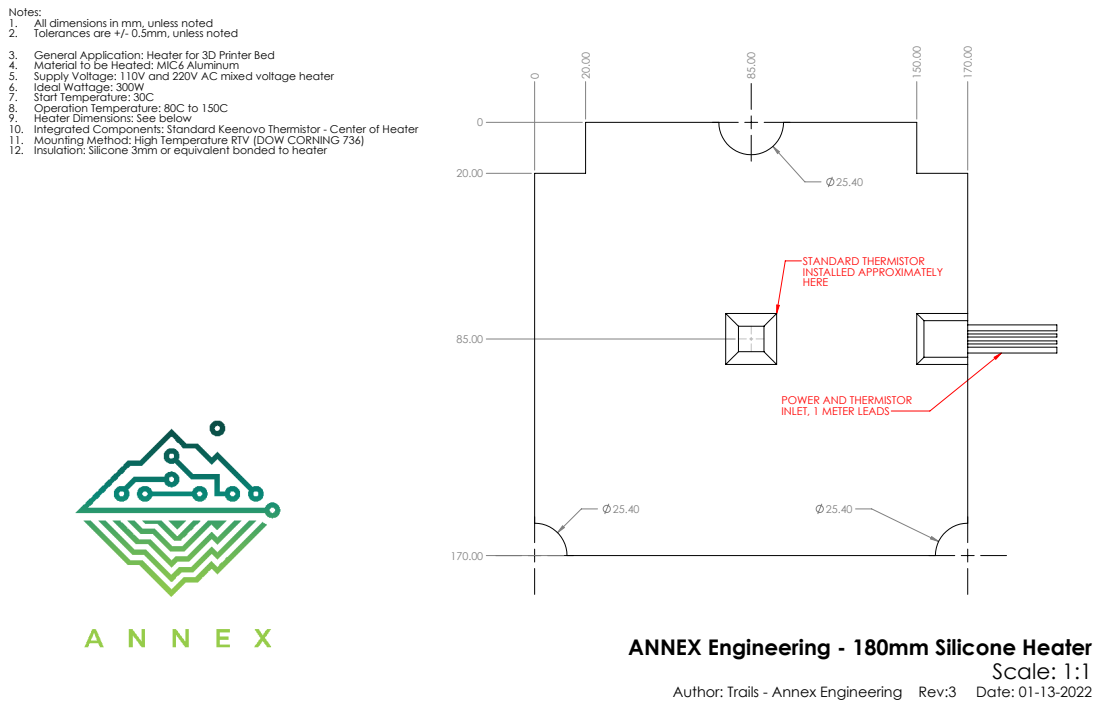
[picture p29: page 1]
STANDARD THERMISTOR INSTALLED APPROXIMATELY; Scale: 1:1

Notes:
1. All dimensions in mm, unless noted
2. Tolerances are +/- 0.5mm, unless noted
3. General Application: Heater for 3D Printer Bed
4. Material to be Heated: MIC6 Aluminum
5. Supply Voltage: 110V and 220V AC mixed voltage heater
6. Ideal Wattage: 300W
7. Start Temperature: 30C
8. Operation Temperature: 80C to 150C
9. Heater Dimensions: See below
10. Integrated Components: Standard Keenovo Thermistor - Center of Heater
11. Mounting Method: High Temperature RTV (DOW CORNING 736)
12. Insulation: Silicone 3mm or equivalent bonded to heater

POWER AND THERMISTOR
INLET, 1 METER LEADS

ANNEX Engineering - 180mm Silicone Heater

Author: Trails - Annex Engineering Rev:3 Date: 01-13-2022

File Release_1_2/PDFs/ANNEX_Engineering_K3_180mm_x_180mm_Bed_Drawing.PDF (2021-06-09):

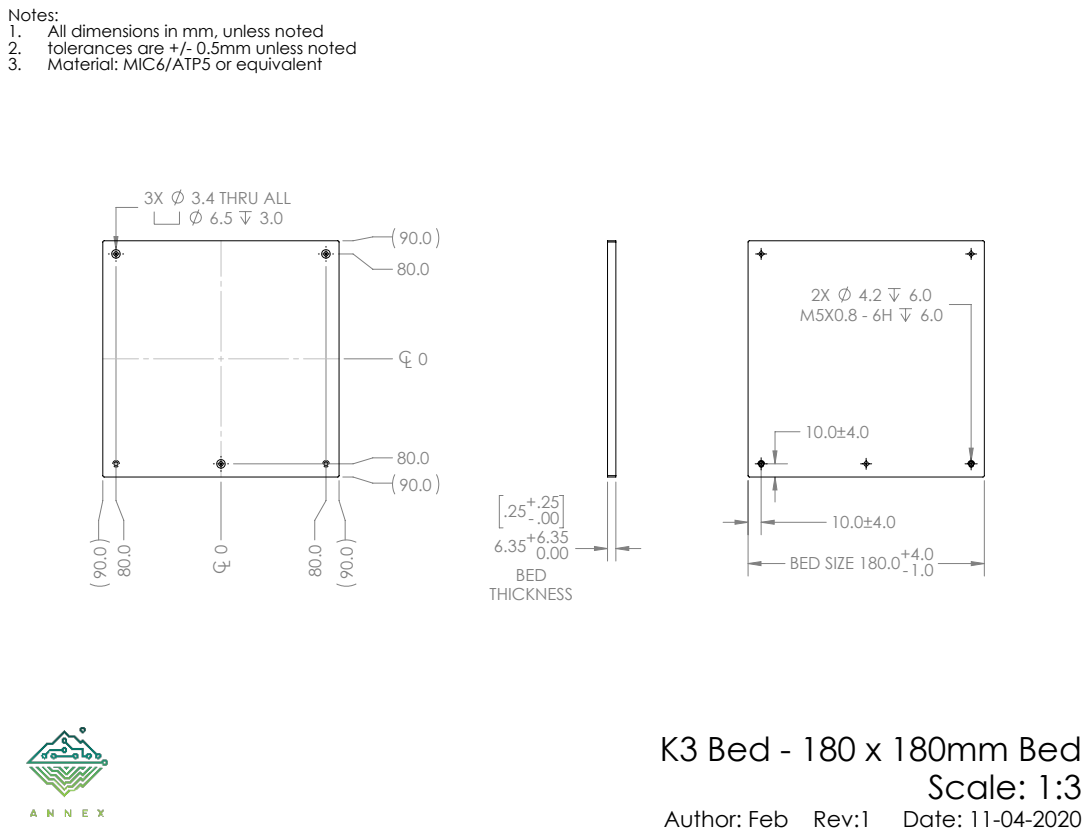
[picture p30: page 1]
3.4 THRU ALL; BED SIZE 180.0+; K3 Bed - 180 x 180mm Bed Scale: 1:3

Notes:
1. All dimensions in mm, unless noted
2. tolerances are +/- 0.5mm unless noted
3. Material: MIC6/ATP5 or equivalent

Author: Feb Rev:1 Date: 11-04-2020

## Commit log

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2021-06-13 add cad for electronics box blanking plate and bed
    [Electronics_Box_Blanking_Plate.STEP, Electronics_Box_Blanking_Plate.x_t, K3_Bed_180x180.x_t]
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2021-06-22 Update edrawing (screws, colors, match newest stls) and fix tophat corner clearance
2021-06-22 Remove old 3Z files and fix print quantities
    [z_drive_2_piece_front_lower_x2_rev2.stl, z_drive_2_piece_front_upper_(6201_option)_x2_rev1.stl, z_drive_2_piece_front_upper_(thrust_option)_x2_rev1.stl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]
2021-06-22 Strengthen and widen the rail guard on the sherpa mini umbilical mount
2021-06-25 Extend dock and wiper arm by 3mm to make the dock easier to reach, and add zip tie holes
    [K3_fysetc_s6_2.0_+_btt_motor_expander_config-180mm_x_180mm_x_180mm_build.cfg, K3_fysetc_spider_config-180mm_x_180mm_x_180mm_build.cfg]
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2021-06-26 Fix dock position error
    [K3_fysetc_s6_2.0_+_btt_motor_expander_config-180mm_x_180mm_x_180mm_build.cfg, K3_fysetc_spider_config-180mm_x_180mm_x_180mm_build.cfg]
2021-06-26 Fix wiper y position to match new y travel
    [K3_fysetc_s6_2.0_+_btt_motor_expander_config-180mm_x_180mm_x_180mm_build.cfg, K3_fysetc_spider_config-180mm_x_180mm_x_180mm_build.cfg]
2021-06-26 Add missing bracket stl
    [frame_center_brace_bracket_x1_rev1.stl]
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2021-07-14 Change and clarify z-motor positions
    Added ASCII diagram for stepper motor positions. Removed incorrect textual references to z-motor positions. Re-ordered z_tilt positions to correspond with new motor numbering.
    [K3_fysetc_s6_2.0_+_btt_motor_expander_config-180mm_x_180mm_x_180mm_build.cfg]
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2021-07-18 Revert "added Belty Belted Z files"
    [Bed_Frame, Maxwell_Rod_and_Safety_Mount_x1_rev1.stl, Z_Drive, Front-Left_x1_rev1.stl, Z_Drive, Front-Right_x1_rev1.stl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]
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2021-08-02 fix uart pin, thanks boa
    [K3_fysetc_spider_config-180mm_x_180mm_x_180mm_build.cfg]
2021-08-03 Fixed front right and rear left motor positions
2021-08-04 Minor changes to multiple settings
    Reversed directions of X and X1 steppers
    Added "homing_retract_dist: 0" for X and Y steppers
    Reduced z homing speed and probe lift speed to match z max_speed
    Added pullup to probe pin
    Reduced heater power from 0.6 to 0.4 to better match recommended 0.4W/cm^2
    Updated RPi temp block from depreciated format
    [K3_fysetc_spider_config-180mm_x_180mm_x_180mm_build.cfg]
2021-08-04 Revert Z homing/probing speeds to 10mm/s
    Also added a comment to potentially increase max_z_velocity after comissioning.
    [K3_fysetc_spider_config-180mm_x_180mm_x_180mm_build.cfg]
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2021-08-09 Add deprecated label to endstops for 1-piece xy motor mounts
    [x180_endstop_12mm_bed_offset_0_+x overtravel_x2_rev1.stl, y0_endstop_0_-Y_overtravel_x2_rev1.stl]
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2021-08-16 wiring grommets are easier to print, assemble and install
    [wiring_grommet_nut_25mm_x3_rev2.STL, wiring_grommet_nut_25mm_x5_rev1.STL, wiring_grommet_nut_35mm_x1_rev2.STL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]
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2021-08-16 strengthen sherpa mini umbilical mount
    [sherpa_umbilical_mount_x1_rev3.stl]
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2021-08-16 Fix cart clearance issue for dragon, dragonfly hic, and dragonfly bms; replace copperhead spacer with a taller brace
    [copperhead_brace_spacer_x1_rev1.stl, dragonfly_hic_fan_spacer_x2_rev1.stl, dragonfly_hic_fan_spacer_x2_rev2.stl]
2021-08-16 Add toolhead for Nitram's VolcoMosq hotend, combine toolhead edrawings into a single file, and update toolhead readme
    [volcomosq_fan_spacer_x2_rev1.stl]
2021-08-16 Fix typo in toolhead readme
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2021-09-02 wrong LRS bracket in folder
    [meanwell_lrs_150_24_psu_mounting_bracket_x2_rev1.STL, universal_meanwell_lrs_psu_mounting_bracket_x2_rev1.STL]
2021-09-02 move 6201 option to the correct folder
    [z_drive_2_piece_front_upper_(6201_option)_mirror_x1_rev1.stl, z_drive_2_piece_front_upper_(6201_option)_x2_rev1.stl]
2021-09-05 Move Triscrew specific files into the correct directory
    [mgn9_mount_front_mirror_x1_rev2.stl, mgn9_mount_front_x1_rev2.stl, mgn9_mount_rear_x1_rev2.stl]
2021-09-06 Update number of moving tensioner parts for beltz + extra
    [xy_tensioner_moving_x8_rev3.stl]
2021-09-07 update klipper configs to standardize on belted z, leadscrew moved to commented out
    update klipper configs to standardize on belted z, leadscrew moved to commented out
    [K3_fysetc_s6_2.0_+_btt_motor_expander_config-180mm_x_180mm_x_180mm_build.cfg, K3_fysetc_spider_config-180mm_x_180mm_x_180mm_build.cfg]
2021-09-07 force M3x16 screw to avoid MGN9C damage
    [xy_tensioner_stationary_mirror_x2_rev2.stl, xy_tensioner_stationary_mirror_x2_rev3.stl, xy_tensioner_stationary_x2_rev2.stl]
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2021-09-16 Fixes #16
    [safety_spring_mount_rear_x1_rev2.stl]
2021-09-19 Fix comment
    [K3_fysetc_spider_config-180mm_x_180mm_x_180mm_build.cfg]
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2021-09-29 fixed Corner Motor Mount for M6 Screw
    [[a]_corner_motor_mount_2_piece_upper_(M6 Corner Screw)_x4_rev3.stl]
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2021-10-15 Add new feet, add brackets for middle bottom extrusion and make printed bracket optional
    [[a]_AMP_foot_decoration_M6_x4_rev1.stl, [a]_AMP_foot_decoration_x4_rev1.stl, [a]_frame_center_brace_bracket_x1_rev1.stl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]
2021-10-22 Fix toolhead clearance on right z_idler
    [[a]_z_idler_front_mirror_x1_rev1.stl, [a]_z_idler_front_x1_rev1.stl]
2021-10-24 Fix comment
    Caused confusion
    [K3_fysetc_spider_config-180mm_x_180mm_x_180mm_build.cfg]
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2021-11-02 fix electronics brackets hole alignment
    [meanwell_lrs_150_24_psu_mounting_bracket_x2_rev1.STL, universal_controller_mounting_bracket_a_x2_rev2.STL, universal_controller_mounting_bracket_a_x2_rev3.STL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]
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2021-11-02 restore missing bracket
    [meanwell_lrs_150_24_psu_mounting_bracket_x2_rev1.STL, universal_meanwell_lrs_psu_mounting_bracket_x2_rev1.STL]
2021-11-19 add 5mm slot options for hinges and magnets
    [front_door_bearing_block_1_(m6_thread)_x2_rev1.STL, front_door_bearing_block_2_(m6_thread)_x2_rev1.STL, front_door_magnet_catch_(m6_thread)_x1_rev1.STL]
2021-11-28 Fix text that should be a comment
    [K3_fysetc_s6_2.0_+_btt_motor_expander_config-180mm_x_180mm_x_180mm_build.cfg]
2021-12-04 Fix screw length for bottom small brackets
2021-12-05 Update example configs w/10t & 8t gear ratios for Sherpa Mini
    [K3_fysetc_s6_2.0_+_btt_motor_expander_config-180mm_x_180mm_x_180mm_build.cfg, K3_fysetc_spider_config-180mm_x_180mm_x_180mm_build.cfg]
2021-12-07 fix rear bed frame mount in netfab
2021-12-10 Improve 8mm shaft fitment and fix #23
    [bed_frame_mount_front_(m6_thread)_mirror_x1_rev2.stl, bed_frame_mount_front_(m6_thread)_x1_rev2.stl, bed_frame_mount_front_mirror_x1_rev2.stl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]
2021-12-13 Add rev 4
    magswitch_probe_mount_x1_rev4 stl errors fixed
    [magswitch_probe_mount_x1_rev4.stl]
2021-12-14 Fix broken stl files
    Fixing the last stl's that did not wanna load in plater.
    [y_min_left_split corner_endstop_x1_rev2.stl]
2021-12-17 make wiring grommet nuts accents instead of primary (looks better)
    [[a]_wiring_grommet_nut_25mm_x5_rev2.STL, [a]_wiring_grommet_nut_35mm_x2_rev2.STL]
2021-12-17 Switch in new maxwell mounts, correct front z idler position, delete duplicate tensioners, separate back panel and spacers into different components, and change grommet nut color
2021-12-24 Fix stress concentration at zip tie mount
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2021-12-26 Add Post Attach Gcode to K3 Klipper Configurations
    Credit to ActualVarner on the Annex Engineering Discord for the changes. I'm just proposing to add them to the repo.
    [K3_fysetc_s6_2.0_+_btt_motor_expander_config-180mm_x_180mm_x_180mm_build.cfg, K3_fysetc_spider_config-180mm_x_180mm_x_180mm_build.cfg]
2022-01-06 Fix macros based on Rivers feedback
    [K3_fysetc_s6_2.0_+_btt_motor_expander_config-180mm_x_180mm_x_180mm_build.cfg, K3_fysetc_spider_config-180mm_x_180mm_x_180mm_build.cfg]
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2022-01-09 Fix comments and make more consistent
    [K3_fysetc_s6_2.0_+_btt_motor_expander_config-180mm_x_180mm_x_180mm_build.cfg, K3_fysetc_spider_config-180mm_x_180mm_x_180mm_build.cfg]
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2022-01-16 Divide purge into smaller chunks to prevent material from sticking out of the bucket
    [K3_fysetc_s6_2.0_+_btt_motor_expander_config-180mm_x_180mm_x_180mm_build.cfg, K3_fysetc_spider_config-180mm_x_180mm_x_180mm_build.cfg]
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2022-01-29 Slightly strengthen mosquito_side_mount and dragon_fan_shroud
    [[a]_mosquito_side_mount_x1_rev4.stl]
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2022-02-08 Make screws extend 3mm into the rail cart instead of 3.4mm to avoid potentially bottoming out the screw if the hole is not deep enough
2022-02-08 - Add magnet rail mounts with square nuts - Add printed cable channels - Correct X/Y rail screw locations to avoid interference between T-nuts - Change wiper clamp screws to BHCS
    [25x40mm_cable_channel_clip_x24_rev1.stl, 6.0mm_rail_xy_cross_rail_mount_mirror_x2_rev2.stl, 6.0mm_rail_xy_cross_rail_mount_mirror_x2_rev3.stl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]
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2022-02-16 Switch to through bolt tensioner spacers, add markings on 6.5mm rail parts
    [6.0mm_rail_xy_tensioner_spacer_x2_rev1.stl, 6.0mm_rail_xy_tensioner_spacer_x2_rev2.stl, xy_cross_rail_mount_mirror_x2_rev3.stl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]
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2022-02-17 Replace cable channel clip with K3 version
    [25x40mm_cable_channel_clip_k3_x24_rev1.stl, 25x40mm_cable_channel_clip_x24_rev1.stl]
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2022-03-11 - Add Sherpa Micro support - Change all M2.5x14 screws to M2.5x16 (affects Dragonfly BMS, Dragonfly BMO, and Rapido, but M2.5x14 still works) - Add dock magnets to toolhead assembly
    [dragonfly_bms_fan_screw_spacer_x1_rev1.stl]
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2022-03-14 Fix unsupported bridges
    [[a]_nozzle_wiper_base_x1_rev4.stl]
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2022-03-22 fix missing fillet
    [electronics_box_blanking_plate_x2_rev1.STL, electronics_box_blanking_plate_x2_rev2.STL]
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2022-04-12 Reverse probe y offset to match edrawing, reverse Z2 stepper
    [K3_fysetc_s6_2.0_+_btt_motor_expander_config-180mm_x_180mm_x_180mm_build.cfg, K3_fysetc_spider_config-180mm_x_180mm_x_180mm_build.cfg]
2022-04-13 added z drives with improved printability, stronger corner bearing holders, and easier hardware sourcing rear z idlers
    [[a]_z_idler_rear_x1_rev1.stl, corner_drive_shaft_support_mirror_x2_rev3.stl, corner_drive_shaft_support_x2_rev3.stl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]
2022-04-13 fixed rear idler z orientation, added updated z brace
    [[a]_z_drive_front_brace_x1_rev1.stl, [a]_z_idler_rear_(lowered)_x1_rev3.stl, [a]_z_idler_rear_x1_rev3.stl]
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2022-04-24 Correct typo in comment
    [K3_fysetc_s6_2.0_+_btt_motor_expander_config-180mm_x_180mm_x_180mm_build.cfg, K3_fysetc_spider_config-180mm_x_180mm_x_180mm_build.cfg]
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2022-05-07 - Add xy shim placement guide in xy_gantry readme - Add protrusion on bucket and matching indentation on wiper base for better alignment - Add M5 spacers for xy corner drives
    [[a]_nozzle_wiper_base_x1_rev5.stl, m5_spacer_x4_rev1.stl]
2022-05-07 Update eDrawing with changes from fecc529 and later, replace large external brackets with small brackets, update belt models to be more accurate at their ends
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2022-06-17 Ensure print_end does not try to move out of bounds, set accel_to_decel same as accel in M204 macro by default
    [K3_fysetc_s6_2.0_+_btt_motor_expander_config-180mm_x_180mm_x_180mm_build.cfg, K3_fysetc_spider_config-180mm_x_180mm_x_180mm_build.cfg]
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2022-07-05 better toleranced slip pins with thru bolts for more stability
    [[a]_tophat_lid_structure_b_x4_rev3.STL, [a]_tophat_lid_structure_b_x4_rev4.STL, tophat_lid_structure_a_x4_rev3.STL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]
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2022-07-10 Add clearance for unthreaded part of M5x25 screw
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2022-07-26 Fix mirror parts
    [Housing_front_alpha_2_micro_x1_Rev1.STL, Party_plate_alpha_2_micro_x1_Rev1.STL, Spacer_alpha_2_micro_x1_Rev1.STL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]
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2022-08-24 retire screw z (may come back in the future with improved design)
    [[a]_frame_center_brace_bracket_x1_rev1.stl, [a]_mgn9_mount_front_mirror_x1_rev2.stl, [a]_mgn9_mount_front_x1_rev2.stl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]
2022-08-28 Add Frostbite support for VolcoMosq, Dragon, and Dragon UHF, and merge left bracket and duct mount into one part
    [[a]_k3_left_bracket_x1_rev1.STL, fan_duct_mount_mgn9c_x1_rev1.STL]
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2022-10-07 fix small interference issue on belted z drive brace
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2022-11-08 Re-add k3rabiner alpha 2 sherpa micro parts from before 882a37e, delete redundant files
    [Housing_front_alpha_2_micro_x1_Rev1.STL, Mirror_core_x1_Rev1.STL, Mirror_housing_rear_nema14_x1_Rev1.STL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]
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2022-11-18 swap nut and screw material colors, in the effort to reduce most primary filament usage under 1kg
    [[a]_wiring_grommet_screw_25mm_x3_rev3.STL, [a]_wiring_grommet_screw_left_35mm_x1_rev4.STL, [a]_wiring_grommet_screw_right_35mm_x1_rev4.STL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]
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2022-11-25 Unhide rail cart Correct toolhead brace screw lengths Swap in new grommets and rev2 backpack cover Update colors to match STL labels
2022-11-25 Thicken top of mosquito brace and add clearance for washers (now matches the part in the edrawing and cad)
    [mosquito_brace_for_probe_mount_x1_rev5.STL]
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2022-11-25 Flip probe y offset again to match edrawing, use value from D2F datasheet
    [K3_fysetc_s6_2.0_+_btt_motor_expander_config-180mm_x_180mm_x_180mm_build.cfg, K3_fysetc_spider_config-180mm_x_180mm_x_180mm_build.cfg]
2022-12-08 Raise frostbite ascender party plate height to 17.5mm to fix screw and rail cart clearance issue
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2022-12-17 Change countersunk magnet screws from M3x10 to M3x12 Fix missing hole in side panel spacers Fix square nut size in left y gantry
2022-12-18 more clearance for longer screw to secure magnet
    [electronics_box_corner_mains_inlet_x1_rev3.STL, electronics_box_corner_mains_inlet_x1_rev4.STL, electronics_box_corner_x3_rev2.STL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]
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2023-02-26 Restore fan speed correctly after wiping
    [K3_fysetc_s6_2.0_+_btt_motor_expander_config-180mm_x_180mm_x_180mm_build.cfg, K3_fysetc_spider_config-180mm_x_180mm_x_180mm_build.cfg]
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2023-03-18 Avoid fragmentation of K3rabiner pcb
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2023-04-20 metal dxfs, for personal use only, vendors must contact for approval
    metal dxfs, for personal use only, vendors must contact for approval
    [K3_2020_Backer_2.6mm_mild_steel_x4_rev1.dxf, corner_motor_mount_ldo_bottom_rev3_x4_6mm.DXF, corner_motor_mount_ldo_top_rev3_x4_3mm.DXF]
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2023-07-15 rename stl correct name
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2025-09-29 Fix clearance for screw connecting teakettle brace and fan shroud outlet
